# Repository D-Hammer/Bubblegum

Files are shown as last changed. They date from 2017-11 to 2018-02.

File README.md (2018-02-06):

# Bubblegum
## Integrated control board

### Scope: 
- Interface with an RC receiver
  - Sbus is priority
  - Other variants will be created later
- Control drive motors
  - 2 motors priority
  - 4 motors later to allow use for Mecanum, etc.
- Control weapon motor
- IMU/PID drive to make up for my lack of driving skill
- Remote adjustable expo, user selectable mixing, sense and remix for inverted driving, remote switch for PID

### To Do
- Test and tune on various drive topologies
- Branch HW and FW to interface w/ standard pwm receivers

# Changelog
## Hardware

### V1.30
- Reduced footprint to 0.94"x0.94"
- Through holes for outputs are now pads to allow for a more compact profile
- 0.8mm FR4, 2oz Cu
- 0.050" pitch programming header

### V1.20
- IMU integrated into control board.  
- 3.3v power system added
- Decreased current capacity on 5V supply to free up board space
- 0.8mm FR4, 2oz Cu

### V1.10
- Increased power input hole diameters

### V1.01
- Rerouted weapon pwm signal to different GPIO
- Added versioning and logo on back silk
- 1.5mm FR4, 1oz Cu

### V1.00
- Prototype
- 0.8mm FR4, 2oz Cu

## Firmware

### 2/6/18
- Minor tweaks to main loop
- Throttle scaling factor added to PID to improve low throttle stability and high throttle tracking
- New boot sequence to communicate with PID tuner
- Library change from SoftwareSerial to NeoSWSerial
- PID Tuner: New, alpha release, programming functions reliably, reading is buggy

### 11/20/17
- Added weapon output to DS branch (servo lib implementation)
- Update PWM branch with DS branch improvements
- New PID gains: P1.8 I0.02 D0.005

### 11/17/17
- Filtered the inversion sensing
- added deadband to PID to stop zero throttle flutter
- PID correction now proportional to throttle input [0.5 + abs(spd)]
- Tuned gains. Settled on P1.2 I0.02 D0.05

### 11/15/17
- Added deadband to drive inputs
- Increased data inclusivity on gyro calibration
- Fixed expo scaling issue
- Fixed sign of gyroOffset in PID
- DShot center is 1048 in 3D mode, NOT 1047 :/

### 11/14/17 
- Added alternate FW for DShot implementation
- dshot fiddlings file uses UART and requires inverter (untested) (DShot150)
- bit banging like an animal is addressable on port D and functional (DShot600)
- New FW syncs ESC update with PID loop and increases frequency from 140 Hz to ~1KHz
- All the standard anti-jitter, digital, checksum goodness you've come to expect from DShot!

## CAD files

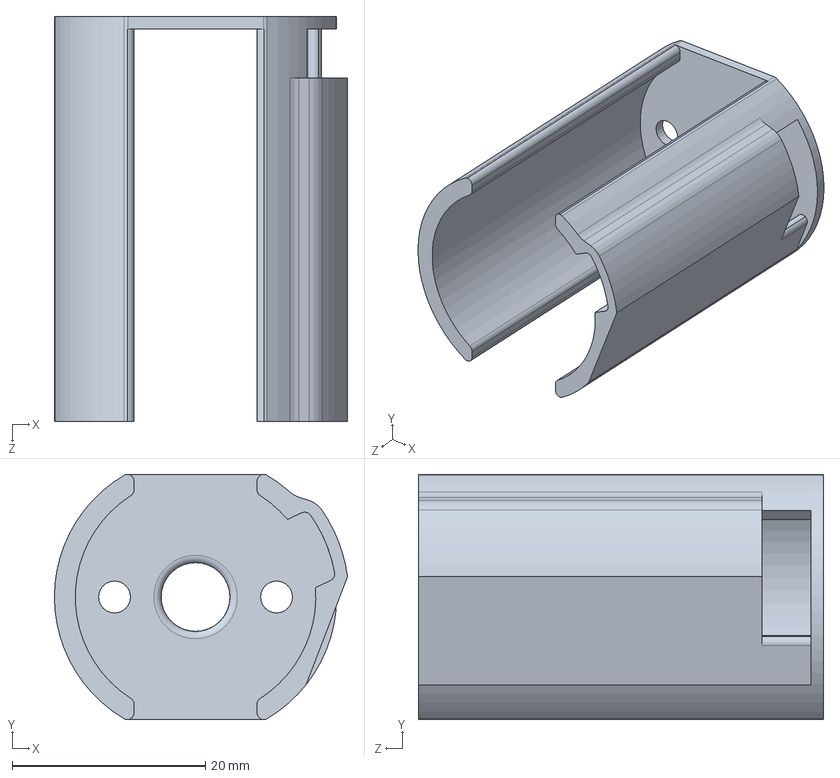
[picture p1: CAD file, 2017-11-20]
CAD/Motor Shroud.SLDPRT
30.3 x 25.4 x 41.9 mm

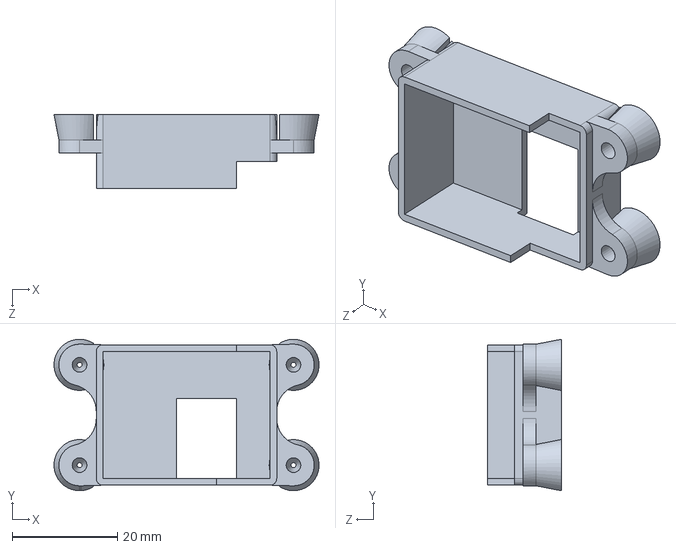
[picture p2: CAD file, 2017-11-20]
CAD/Bubblegum Box.SLDPRT
50.3 x 28.8 x 14.0 mm

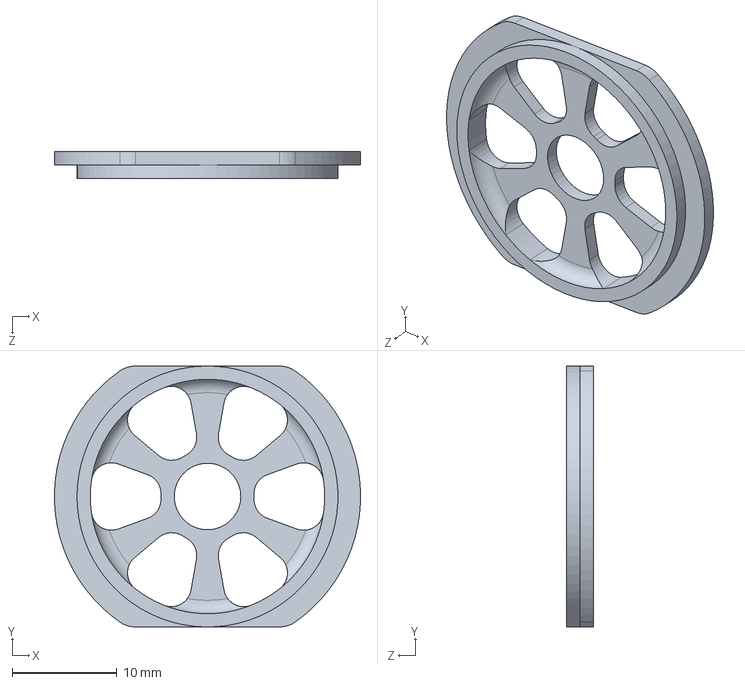
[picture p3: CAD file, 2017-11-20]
CAD/Motor Shroud Cap.SLDPRT
29.2 x 24.9 x 2.54 mm

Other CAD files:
CAD/Motor Shroud Mirror.SLDPRT

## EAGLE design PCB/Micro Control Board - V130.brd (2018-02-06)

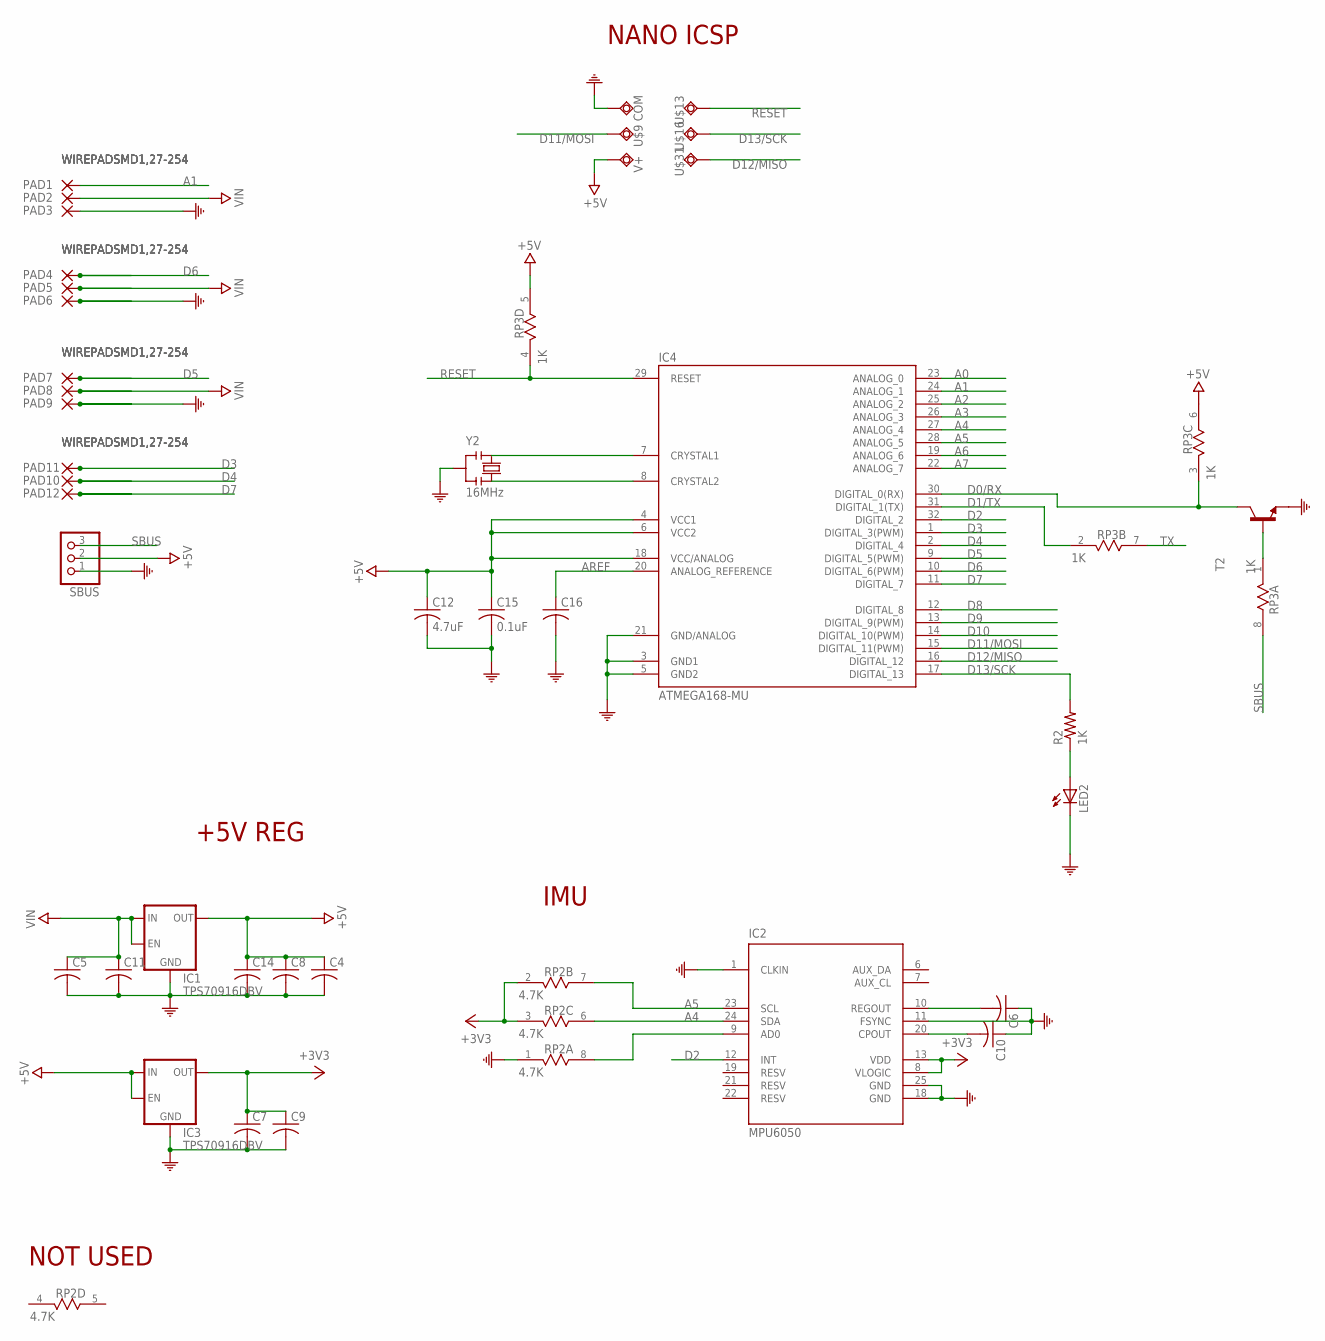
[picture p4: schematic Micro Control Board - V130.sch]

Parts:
C4, C5, C6, C7, C8, C9, C10, C11, C14, C16: C-USC0402; C0402
C12: 4.7uF; C0402
C15: 0.1uF; C0402
COM: 0.7MM-THRU; 0.65MM-THRU
IC1, IC3: TPS70916DBV; SOT23-5
IC2: MPU6050; QFN50P400X400X95-25T265X275N
IC4: ATMEGA168-MU; MLF32
LED2: LEDCHIP-LED0603; CHIP-LED0603
PAD1, PAD2, PAD3, PAD4, PAD5, PAD6, PAD7, PAD8, PAD9, PAD10, PAD11, PAD12: WIREPADSMD1,27-254; SMD1,27-2,54
R2: 1K; R0402
RP2: 4.7K; RES4NT
RP3: 1K; RES4NT
SBUS: PINHD-1X3; 1X03
T2: MMBT3904LT1-NPN-SOT23-BEC; SOT23-BEC
U$9, U$13, U$16, U$31: 0.7MM-THRU; 0.65MM-THRU
V+: 0.7MM-THRU; 0.65MM-THRU
Y2: 16MHz; RESONATOR

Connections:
+3V3: C7.1, C9.1, IC2.8 (VLOGIC), IC2.13 (VDD), IC3.5 (OUT), RP2.2 (1), RP2.3 (1)
+5V: C4.1, C8.1, C12.1, C14.1, C15.1, IC1.5 (OUT), IC3.1 (IN), IC3.3 (EN), IC4.4 (VCC1), IC4.6 (VCC2), IC4.18 (VCC/ANALOG), RP3.5 (2), RP3.6 (2), SBUS.2, V+.P$2
A0: IC4.23 (ANALOG_0)
A1: IC4.24 (ANALOG_1), PAD1.1
A2: IC4.25 (ANALOG_2)
A3: IC4.26 (ANALOG_3)
A4: IC2.24 (SDA), IC4.27 (ANALOG_4), RP2.6 (2)
A5: IC2.23 (SCL), IC4.28 (ANALOG_5), RP2.7 (2)
A6: IC4.19 (ANALOG_6)
A7: IC4.22 (ANALOG_7)
AREF: C16.1, IC4.20 (ANALOG_REFERENCE)
COM: C4.2, C5.2, C6.1, C7.2, C8.2, C9.2, C10.1, C11.2, C12.2, C14.2, C15.2, C16.2, COM.P$2, IC1.2 (GND), IC2.1 (CLKIN), IC2.11 (FSYNC), IC2.18 (GND), IC2.25 (GND), IC3.2 (GND), IC4.3 (GND1), IC4.5 (GND2), IC4.21 (GND/ANALOG), LED2.C, PAD3.1, PAD6.1, PAD9.1, RP2.1, SBUS.1, T2.E, Y2.2
D0/RX: IC4.30 (DIGITAL_0(RX)), RP3.3 (1), T2.C
D1/TX: IC4.31 (DIGITAL_1(TX)), RP3.2 (1)
D2: IC2.12 (INT), IC4.32 (DIGITAL_2)
D3: IC4.1 (DIGITAL_3(PWM)), PAD10.1
D4: IC4.2 (DIGITAL_4), PAD11.1
D5: IC4.9 (DIGITAL_5(PWM)), PAD7.1
D6: IC4.10 (DIGITAL_6(PWM)), PAD4.1
D7: IC4.11 (DIGITAL_7), PAD12.1
D8: IC4.12 (DIGITAL_8)
D9: IC4.13 (DIGITAL_9(PWM))
D10: IC4.14 (DIGITAL_10(PWM))
D11/MOSI: IC4.15 (DIGITAL_11(PWM)), U$9.P$2
D12/MISO: IC4.16 (DIGITAL_12), U$31.P$2
D13/SCK: IC4.17 (DIGITAL_13), R2.2, U$16.P$2
unnamed: IC2.9 (AD0), RP2.8 (2)
unnamed: C6.2, IC2.10 (REGOUT)
unnamed: IC4.7 (CRYSTAL1), Y2.1
unnamed: C10.2, IC2.20 (CPOUT)
unnamed: IC4.8 (CRYSTAL2), Y2.3
unnamed: LED2.A, R2.1
unnamed: RP3.1, T2.B
RESET: IC4.29 (RESET), RP3.4 (1), U$13.P$2
SBUS: RP3.8 (2), SBUS.3
TX: RP3.7 (2)
VIN: C5.1, C11.1, IC1.1 (IN), IC1.3 (EN), PAD2.1, PAD5.1, PAD8.1

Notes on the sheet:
+5V REG
NANO ICSP
NOT USED
IMU

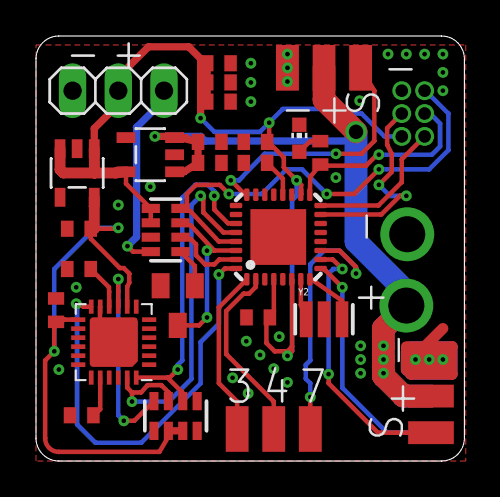
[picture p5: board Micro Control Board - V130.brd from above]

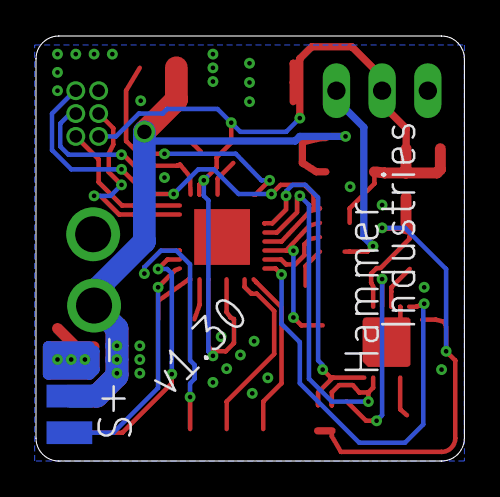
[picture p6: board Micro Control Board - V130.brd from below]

Board: 2 copper layers, 23.8 x 23.6 mm, 41 parts (3 on the bottom side), 28 nets.

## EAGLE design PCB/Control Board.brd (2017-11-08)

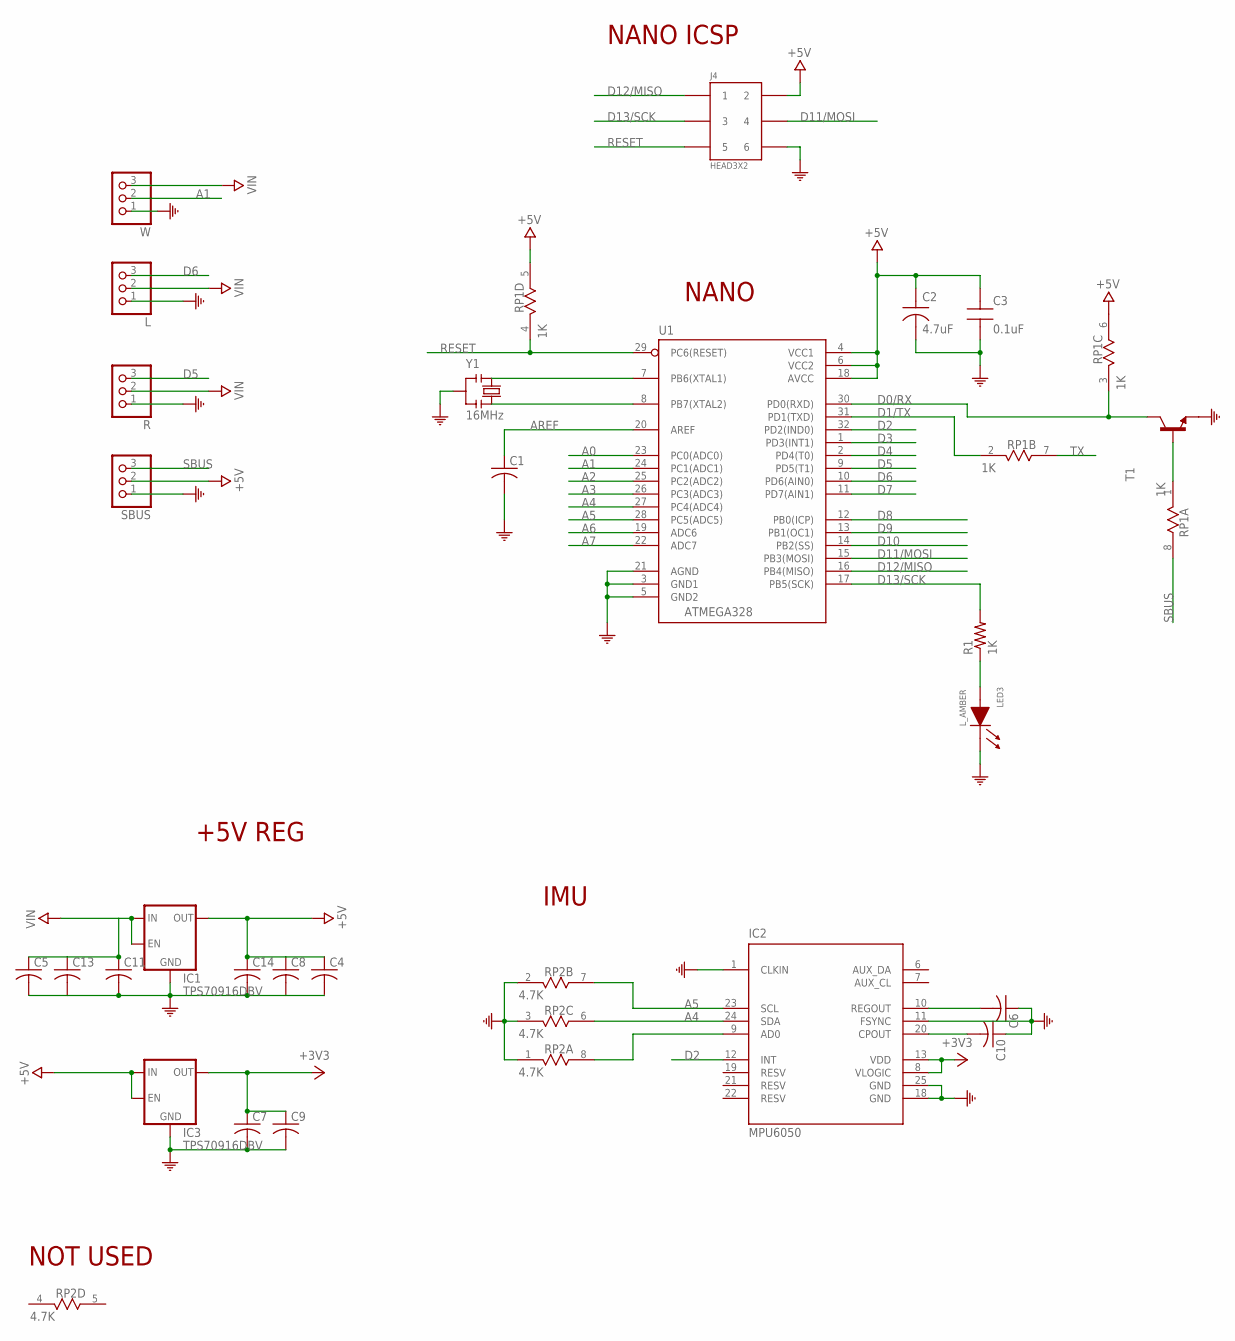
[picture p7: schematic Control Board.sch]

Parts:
C1, C4, C5, C6, C7, C8, C9, C10, C11, C13, C14: C-USC0603; C0603
C2: 4.7uF; TAN-A
C3: 0.1uF; CAP0805-NP
IC1, IC3: TPS70916DBV; SOT23-5
IC2: MPU6050; QFN50P400X400X95-25T265X275N
J4: HEAD3X2
L: PINHD-1X3; 1X03
LED3: L_AMBER; LED0805
R: PINHD-1X3; 1X03
R1: 1K; R0603
RP1: 1K; RES4NT
RP2: 4.7K; RES4NT
SBUS: PINHD-1X3; 1X03
T1: MMBT3904LT1-NPN-SOT23-BEC; SOT23-BEC
U1: ATMEGA328; QFP032
W: PINHD-1X3; 1X03
Y1: 16MHz; RESONATOR

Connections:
+3V3: C7.1, C9.1, IC2.8 (VLOGIC), IC2.13 (VDD), IC3.5 (OUT)
+5V: C2.1, C3.1, C4.1, C8.1, C14.1, IC1.5 (OUT), IC3.1 (IN), IC3.3 (EN), J4.2, RP1.5 (2), RP1.6 (2), SBUS.2, U1.4 (VCC1), U1.6 (VCC2), U1.18 (AVCC)
A0: U1.23 (PC0(ADC0))
A1: U1.24 (PC1(ADC1)), W.2
A2: U1.25 (PC2(ADC2))
A3: U1.26 (PC3(ADC3))
A4: IC2.24 (SDA), RP2.6 (2), U1.27 (PC4(ADC4))
A5: IC2.23 (SCL), RP2.7 (2), U1.28 (PC5(ADC5))
A6: U1.19 (ADC6)
A7: U1.22 (ADC7)
AREF: C1.1, U1.20 (AREF)
COM: C1.2, C2.2, C3.2, C4.2, C5.2, C6.1, C7.2, C8.2, C9.2, C10.1, C11.2, C13.2, C14.2, IC1.2 (GND), IC2.1 (CLKIN), IC2.11 (FSYNC), IC2.18 (GND), IC2.25 (GND), IC3.2 (GND), J4.6, L.1, LED3.1 (CA), R.1, RP2.1, RP2.2 (1), RP2.3 (1), SBUS.1, T1.E, U1.3 (GND1), U1.5 (GND2), U1.21 (AGND), W.1, Y1.2
D0/RX: RP1.3 (1), T1.C, U1.30 (PD0(RXD))
D1/TX: RP1.2 (1), U1.31 (PD1(TXD))
D2: IC2.12 (INT), U1.32 (PD2(IND0))
D3: U1.1 (PD3(INT1))
D4: U1.2 (PD4(T0))
D5: R.3, U1.9 (PD5(T1))
D6: L.3, U1.10 (PD6(AIN0))
D7: U1.11 (PD7(AIN1))
D8: U1.12 (PB0(ICP))
D9: U1.13 (PB1(OC1))
D10: U1.14 (PB2(SS))
D11/MOSI: J4.4, U1.15 (PB3(MOSI))
D12/MISO: J4.1, U1.16 (PB4(MISO))
D13/SCK: J4.3, R1.2, U1.17 (PB5(SCK))
unnamed: U1.8 (PB7(XTAL2)), Y1.3
unnamed: U1.7 (PB6(XTAL1)), Y1.1
unnamed: IC2.9 (AD0), RP2.8 (2)
unnamed: C6.2, IC2.10 (REGOUT)
unnamed: RP1.1, T1.B
unnamed: C10.2, IC2.20 (CPOUT)
unnamed: LED3.2 (AN), R1.1
RESET: J4.5, RP1.4 (1), U1.29 (PC6(RESET))
SBUS: RP1.8 (2), SBUS.3
TX: RP1.7 (2)
VIN: C5.1, C11.1, C13.1, IC1.1 (IN), IC1.3 (EN), L.2, R.2, W.3

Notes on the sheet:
NANO
+5V REG
NANO ICSP
NOT USED
IMU

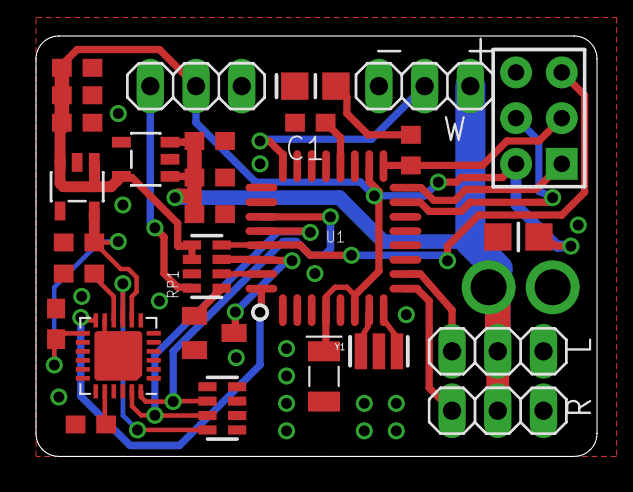
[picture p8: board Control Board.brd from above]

Board: 2 copper layers, 31.2 x 23.4 mm, 28 parts (0 on the bottom side), 25 nets.

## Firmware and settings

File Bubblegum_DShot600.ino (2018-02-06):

#include <Wire.h>
#include <Servo.h>
#include <FUTABA_SBUS.h> // Source: http://www.ernstc.dk/arduino/sbus.html
#include <EEPROM.h>
#define debug 0 // Serial debug mode, 0 for off, 1 for on
#include <NeoSWSerial.h> // For debugging and programming

////////// Create instances //////////
#if debug
NeoSWSerial mserial(10, 11); // RX, TX (serial for debug)
#endif
NeoSWSerial pserial(11, 12); // RX, TX (serial for programmer)
FUTABA_SBUS sBus;                 // sBus over serial
Servo WeaponOUT;                  // Weapon output

////////// IMU Data //////////
double accX, accY, accZ;
double gyroX, gyroY, gyroZ;
int16_t tempRaw;
uint32_t timer;
uint8_t i2cData[14]; // Buffer for I2C data
double gyroBuffer[5]; // Buffer for gyro low pass filter
double fGyro, gyroOffset;  // Filtered gyro value and gyro calibration offset
uint8_t i;

////////// Control Vars //////////
double expovalThrottle = 0.25;
uint8_t deadband = 15;
uint8_t inversionCounter;

////////// Pid Vars //////////
uint16_t Pi, Ii, Di; // Scaled values, max is 65535
double Kp = 1.81, Ki = 0.02, Kd = 0.005;
double P0, P, I, D;
int16_t maxSpin = 500; // Degrees per second, Remember to set gyro scale register accordingly
uint8_t S, progInstruct; // Throttle scaling factor

////////// DShot Vars //////////
int16_t dShotVal = 0; // Initialize in disarm status, valid vals: 48-2047
uint8_t pin = 32; // Right wheel is 32, Left wheel is 64

void setup() {
#if debug
  mserial.begin(9600); // Pour a bowl of Serial. Begins debug serial com
#endif


  ///// PID Programming /////
  pserial.begin(9600);
  pinMode(12, OUTPUT);
  initialize();
  while (pserial.available() == 0 && i < 100) {
    i++;
    delay(1);
  }
  i = 0;
  if (pserial.available() > 0) progInstruct = pserial.read();
  if (progInstruct == 4) {
    receiveData();
  }
  sendData();


  ///// Normal Startup /////
  sBus.begin();
  Wire.begin();          // Begins I2C for IMU
  Wire.setClock(400000UL); // Set I2C frequency to 400kHz


  pinMode(13, OUTPUT);  // Indicator LED
  digitalWrite(13, 1);
  delay(1000);
  digitalWrite(13, 0); // Indicator LED off


#if debug
  mserial.println("POST");
#endif


  i2cData[0] = 7; // Set the sample rate to 1000Hz - 8kHz/(7+1) = 1000Hz
  i2cData[1] = 0x00; // Disable FSYNC and set 260 Hz Acc filtering, 256 Hz Gyro filtering, 8 KHz sampling
  i2cData[2] = 0x18; // Set Gyro Full Scale Range to ±500deg/s
  i2cData[3] = 0x00; // Set Accelerometer Full Scale Range to ±2g
  while (i2cWrite(0x19, i2cData, 4, false)); // Write to all four registers at once
  while (i2cWrite(0x1B, 0x10, true));
  while (i2cWrite(0x6B, 0x01, true)); // PLL with X axis gyroscope reference and disable sleep mode
  while (i2cRead(0x75, i2cData, 1));


  delay(100); // Wait for sensor to stabilize
  while (i < 150) { // Calibrate gyro
    while (i2cRead(0x47, i2cData, 2)); // Read value
    gyroZ = (i2cData[0] << 8) | i2cData[1];
    if (gyroZ < 2500 && gyroZ > -2500) { // Save value if not moving too much
      i += 1;
      gyroOffset += gyroZ;
    }
    transmit_dShot(0, 32);
    transmit_dShot(0, 64);
    delay(30);
  }
  i = 0;
  gyroOffset = gyroOffset / 150.0 / 131.0; // Average over 100 values and scale to deg/s


  digitalWrite(13, 1);

  WeaponOUT.attach(15);
  for (uint16_t i = 0; i < 500; i++) { // Initialize the drive in unarmed state
    transmit_dShot(dShotVal, 32);
    transmit_dShot(dShotVal, 64);
    delay(10);
  }

  timer = micros();
}

void loop() {

  // SBUS in
  sBus.FeedLine();
  if (sBus.toChannels == 1) {
    sBus.UpdateServos();
    sBus.UpdateChannels();
    sBus.toChannels = 0;
  }


  // Expo
  double expo;
  expo = (double)(sBus.channels[4] - 172) / 1640.0; // Ch5 sets expo %
  double ch1 = (sBus.channels[1] - 991.5) / 820.0; // Apply expo
  ch1 = expo * ch1 * ch1 * ch1 + (1.0 - expo) * ch1;
  double ch2 = (sBus.channels[2] - 991.5) / 820.0;
  ch2 = expovalThrottle * ch2 * ch2 * ch2 + (1.0 - expovalThrottle) * ch2; // Added separate expo val for forward/reverse 12/24/17 per Matt & Brit feedback



  // Mixing
  // Determine desired movement
  double spd, clockwise_spin;
  if (sBus.channels[5] > 1600) { // Ch6 toggles between straight and diagonal drive
    spd = (ch2 - ch1) / 2.0; // Diagonal mix
    clockwise_spin = (ch2 + ch1) / 2.0;
  } else { // Straight
    spd = ch2;
    clockwise_spin = ch1;
  }


  // Upside down reversing
  if (accZ < -11000) { // If sensor says 3/4ish upside down or more
    if (inversionCounter < 200) inversionCounter++; // if buffer isn't saturated then increment
  }
  else {
    if (inversionCounter > 0) inversionCounter--; // if not upside down and buffer isn't zero'd then decrement
  }
  if (inversionCounter > 100) { // if buffer shows we're upside down a lot recently then invert controls
    spd = -spd;
  }


  /* Update all the values */
  while (i2cRead(0x3B, i2cData, 14));
  //accX = ((i2cData[0] << 8) | i2cData[1]); // We don't care about these commented out datas presently
  //accY = ((i2cData[2] << 8) | i2cData[3]);
  accZ = ((i2cData[4] << 8) | i2cData[5]);
  //tempRaw = (i2cData[6] << 8) | i2cData[7];
  //gyroX = (i2cData[8] << 8) | i2cData[9];
  //gyroY = (i2cData[10] << 8) | i2cData[11];
  gyroZ = (i2cData[12] << 8) | i2cData[13];

  double dt = (double)(micros() - timer) / 1000000; // Calculate delta time
  timer = micros();

  // Lowpass filter the gyro
  i += 1;
  if (i > 4) i = 0;
  gyroBuffer[i] = gyroZ;
  fGyro = (gyroBuffer[0] + gyroBuffer[1] + gyroBuffer[2] + gyroBuffer[3] + gyroBuffer[4]) / 5;


  // PID
  if (sBus.channels[6] > 1600) { // Ch7 toggles PID on/off
    clockwise_spin = clockwise_spin * maxSpin; // Rescale from % to degrees/sec
    if (abs(clockwise_spin) * 2 < 1) clockwise_spin = 0; // Deadband
    P0 = P;
    if (inversionCounter > 100) { // No death spirals!
      P = clockwise_spin - (fGyro / 131.0 - gyroOffset);
    } else {
      P = clockwise_spin + (fGyro / 131.0 - gyroOffset); // P is error, 131 scales to deg/s for sensitivity of 250, add calibration
    }
    if (abs(P) < 10 && abs(spd) < 0.02) P = 0; // PID deadband to prevent zero throttle jittering
    I += P * dt;
    D = (P - P0) / dt;
    clockwise_spin = (clockwise_spin + (S / 100.0 + abs(spd)) * (Kp * P + Ki * I + Kd * D)) / maxSpin; // Apply PID and rescale back to %
  }


  // Convert from spd and cws to wheel outputs
  if (spd - clockwise_spin < 0) {
    ch1 = (spd - clockwise_spin + 1.0) * -999.0 + 1047;
    if (ch1 > 1047) ch1 = 1047;
    if (ch1 < 48 + deadband) ch1 = 1048;
  }
  else {
    ch1 = (spd - clockwise_spin) * 999.0 + 1048;
    if (ch1 > 2047) ch1 = 2047;
    if (ch1 < 1048 + deadband) ch1 = 1048;
  }
  if (spd + clockwise_spin < 0) {
    ch2 = (spd + clockwise_spin + 1.0) * -999.0 + 1047;
    if (ch2 > 1047) ch2 = 1047;
    if (ch2 < 48 + deadband) ch2 = 1048;
  }
  else {
    ch2 = (spd + clockwise_spin) * 999.0 + 1048;
    if (ch2 > 2047) ch2 = 2047;
    if (ch2 < 1048 + deadband) ch2 = 1048;
  }


  // Update outputs
  dShotVal = ch1; pin = 32; // Right wheel, ch1
  transmit_dShot(dShotVal, pin);
  dShotVal = ch2; pin = 64; // Left wheel, ch2
  transmit_dShot(dShotVal, pin);
  WeaponOUT.writeMicroseconds(map(sBus.channels[0], 172, 1811, 1000, 2000)); // Output weapon motor signal
}

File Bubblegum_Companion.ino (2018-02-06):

/*
   Control software for the Bubblegum Companion PID programmer

                                             By D.Hammer
*/
#include <NeoSWSerial.h>
#include <LiquidCrystal.h>
#include <EEPROM.h>
#define debug 0 // Serial debug mode, 0 for off, 1 for on
//#include <SoftwareSerial.h>

////////// Create instances //////////
LiquidCrystal lcd(12, 11, 5, 4, 3, 2);
NeoSWSerial mserial(15, 18); // RX, TX

////////// Vars //////////
uint8_t mode = 6; // What mode are we in? 0-P, 1-I, 2-D, 3-S, 4-Read, 5-Reset
uint16_t Pi, Ii, Di; // Scaled values, max is 65535
double P, I, D; // Unscaled values, Xi/1000.0
uint8_t S; // Throttle scaling factor
uint8_t longPressVal;
uint16_t delayInterval = 500;

void setup() {
  Serial.begin(9600);
  mserial.begin(9600); // Pour a bowl of Serial. Begins serial com

  analogWrite(10, 100);
  lcd.begin(16, 2); // Number of columns, rows
  lcd.setCursor(0, 0);
  lcd.write("     Hammer");
  lcd.setCursor(0, 1);
  lcd.write("   Industries");

  initialize();

  pinMode(6, INPUT_PULLUP); // Enter/send
  pinMode(7, INPUT_PULLUP); // Left
  pinMode(8, INPUT_PULLUP); // Mode
  pinMode(9, INPUT_PULLUP); // Right
  pinMode(15, INPUT_PULLUP); // Prevent floating
  pinMode(16, INPUT_PULLUP); // Prevent floating
  pinMode(17, OUTPUT); // Reset line
  digitalWrite(17, HIGH);

  delay(2000);
  lcd.clear();
}

void loop() {
  Serial.println(digitalRead(8));
  if (digitalRead(6) == 0) { // Enter/send
    if (mode < 4) {
      save();
      transmitData();
    }
    else if (mode == 4) {
      requestData();
      save();
    }
    else {
      EEPROM.write(0, 0); // Reset the initialized token
      initialize();
      mode = 6;
    }
    while (digitalRead(6) == 0);
  }
  else if (digitalRead(8) == 0 || mode > 5) { // Mode
    mode ++;
    if (mode > 5) {
      mode = 0;
      lcd.clear();
      lcd.blink();
      lcd.setCursor(0, 0);
      lcd.print("P:       I:     ");
      lcd.setCursor(2, 0);
      lcd.print(P, 3);
      lcd.setCursor(11, 0);
      lcd.print(I, 3);
      lcd.setCursor(0, 1);
      lcd.print("D:       S:");
      lcd.setCursor(2, 1);
      lcd.print(D, 3);
      lcd.setCursor(11, 1);
      lcd.print(S);
      lcd.setCursor(0, 0);
    }
    if (mode == 1) lcd.setCursor(9, 0);
    if (mode == 2) lcd.setCursor(0, 1);
    if (mode == 3) lcd.setCursor(9, 1);
    if (mode == 4) {
      lcd.clear();
      lcd.print("   Read from");
      lcd.setCursor(0, 1);
      lcd.print("   target?");
      lcd.noBlink();
    }
    if (mode == 5) {
      lcd.clear();
      lcd.print("  Reset vars?");
      lcd.noBlink();
    }
    delay(50);
    while (digitalRead(8) == 0);
  }
  else if (digitalRead(9) == 0) { // Left
    if (longPressVal < 10) longPressVal++;
    if (mode == 0) {
      Pi--;
      if (Pi < 0) Pi = 0;
      P = Pi / 1000.0;
      lcd.setCursor(2, 0);
      lcd.print(P, 3);
      lcd.setCursor(0, 0);
    }
    if (mode == 1) {
      Ii--;
      if (Ii < 0) Ii = 0;
      I = Ii / 1000.0;
      lcd.setCursor(11, 0);
      lcd.print(I, 3);
      lcd.setCursor(9, 0);
    }
    if (mode == 2) {
      Di--;
      if (Di < 0) Di = 0;
      D = Di / 1000.0;
      lcd.setCursor(2, 1);
      lcd.print(D, 3);
      lcd.setCursor(0, 1);
    }
    if (mode == 3) {
      if (S > 0) S--;
      lcd.setCursor(11, 1);
      lcd.print(S);
      lcd.setCursor(9, 1);
    }
    delayInterval = 500 - 50 * longPressVal + 1;
    delay(delayInterval);
  }
  else if (digitalRead(7) == 0) { // Right
    if (longPressVal < 10) longPressVal++;
    if (mode == 0) {
      Pi++;
      if (Pi > 50000) Pi = 50000;
      P = Pi / 1000.0;
      lcd.setCursor(2, 0);
      lcd.print(P, 3);
      lcd.setCursor(0, 0);
    }
    if (mode == 1) {
      Ii++;
      if (Ii > 10000) Ii = 10000;
      I = Ii / 1000.0;
      lcd.setCursor(11, 0);
      lcd.print(I, 3);
      lcd.setCursor(9, 0);
    }
    if (mode == 2) {
      Di++;
      if (Di > 50000) Di = 50000;
      D = Di / 1000.0;
      lcd.setCursor(2, 1);
      lcd.print(D, 3);
      lcd.setCursor(0, 1);
    }
    if (mode == 3) {
      S++;
      if (S > 100) S = 100;
      lcd.setCursor(11, 1);
      lcd.print(S);
      lcd.setCursor(9, 1);
    }
    delayInterval = 500 - 50 * longPressVal + 1;
    delay(delayInterval);
  }
  else longPressVal = 1;
  delayInterval = 500 - 50 * longPressVal + 1;
  delay(1);
}

void transmitData() {
  digitalWrite(17, LOW); // Reset target
  lcd.clear();
  lcd.write("Transmitting...");
  delay(1);
  digitalWrite(17, HIGH); // Start target
  delay(90);
  mserial.write(4);

  delay(1);
  mserial.write(highByte(Pi));
  mserial.write(lowByte(Pi));
  mserial.write(highByte(Ii));
  mserial.write(lowByte(Ii));
  mserial.write(highByte(Di));
  mserial.write(lowByte(Di));
  mserial.write(S);
 
  delay(100);
  lcd.setCursor(0, 1);
  lcd.write("Done.");
  delay(1000);
  
  mserial.read(); // Target transmits even on send, reading to flush serial buffer
  mserial.read();
  mserial.read();
  mserial.read();
  mserial.read();
  mserial.read();
  mserial.read();
  
  mode = 6; // Return
}

void requestData() {
  digitalWrite(17, LOW); // Reset target
  lcd.clear();
  lcd.write("Requesting...");
  delay(1);
  digitalWrite(17, HIGH); // Start target
  delay(90);
  mserial.write(11);

  uint16_t i = 0;
  while (mserial.available() < 7 && i < 5000) {
    i++;
    delay(1);
  }
  lcd.setCursor(0, 1);
  if (i < 5000) {
    Pi = mserial.read() << 8 | mserial.read();
    Ii = mserial.read() << 8 | mserial.read();
    Di = mserial.read() << 8 | mserial.read();
    S = mserial.read();
    P = Pi / 1000.0; // Scale values for use
    I = Ii / 1000.0;
    D = Di / 1000.0;
    lcd.write("Done.");
  }
  else {
    lcd.write("Failed.");
    delay(2000);
  }
  delay(1000);
  mode = 6;
}

void initialize() {
  uint8_t memIsInitialized = EEPROM.read(0);
  if (memIsInitialized == 0) { // If the EEPROM is empty
    EEPROM.write(1, 0x07); // High and low bits for Pi, Ii, and Di in hex
    EEPROM.write(2, 0x08);
    EEPROM.write(3, 0x00);
    EEPROM.write(4, 0x14);
    EEPROM.write(5, 0x00);
    EEPROM.write(6, 0x05);
    EEPROM.write(7, 30);
    EEPROM.write(0, 1); // Set as initialized
  }
  Pi = EEPROM.read(1) << 8 | EEPROM.read(2); // Read values from EEPROM
  Ii = EEPROM.read(3) << 8 | EEPROM.read(4);
  Di = EEPROM.read(5) << 8 | EEPROM.read(6);
  S = EEPROM.read(7);
  P = Pi / 1000.0;
  I = Ii / 1000.0;
  D = Di / 1000.0;
}

void save() {
  EEPROM.write(1, highByte(Pi)); // High and low bits for Pi, Ii, and Di in hex
  EEPROM.write(2, lowByte(Pi));
  EEPROM.write(3, highByte(Ii));
  EEPROM.write(4, lowByte(Ii));
  EEPROM.write(5, highByte(Di));
  EEPROM.write(6, lowByte(Di));
  EEPROM.write(7, S);
}

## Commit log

2017-11-20 Rename Control Board.brd to PCB/Control Board.brd
    [Control Board.brd]
2017-11-20 Rename Control Board.sch to PCB/Control Board.sch
    [Control Board.sch]
